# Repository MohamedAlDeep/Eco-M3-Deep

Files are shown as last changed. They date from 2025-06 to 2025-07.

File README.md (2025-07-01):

# Eco M3 Deep
It is my custom built 3D printer, with all custom 3D printed parts with large bed area.

I made this printer as it would help in making other projects as i don't have direct access to one, and i am interested more on hackclub events projects & science projects which constantly need custom 3D printed parts.

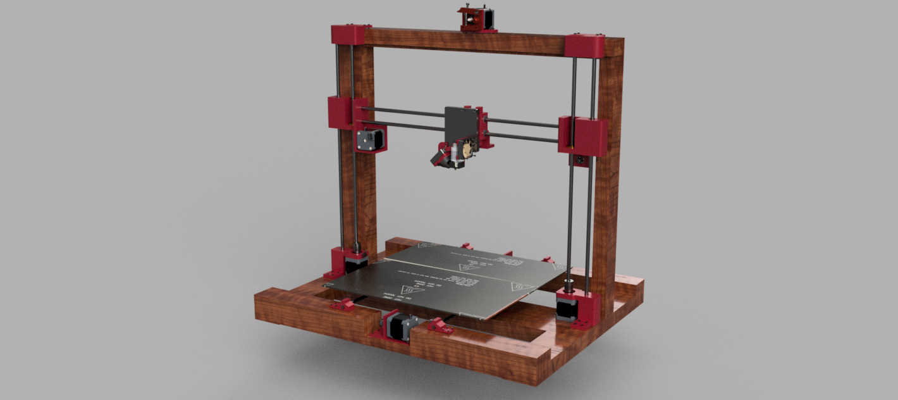
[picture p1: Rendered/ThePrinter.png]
The Printer


## Features 
    - Simplicity
    - Large Bed size with area of 40cmx40cm
    - Remote Extruder
    - The structure & large bed mount are made from wood to reduce cost
    - Expandable design for future additions

## Assembly
1. Mounts 

    - It is simple, start by putting linear bearings into the mounts specifically the moving z axis and the hotend mounts. 
2. Attachments
    -  Screw the hotend
    - Attach mechanical stops with the y axis motor, the same applies to the z axis bottom mount.
    - Screw the x axis bed motor onto its place.
    - Add the pulleys onto the motors shafts and onto a 3D printed small 8mm shaft that is connected to a 8mm bearing.
3. Structure
    - Make 7x 2x3cm wooden part with length of 50cm, put them together as in the image.
4. Axes assembly
    - Z axis
        - Connect the bottom z axis motor to the coupler and the coupler to the T8 lead screw.
        - Connect the T8 screw nut onto its place on the movable z axis middle mount.
        - Connect the upper z mount that has an 8mm bearing into the T8 screw.
        - Stabalize the structure by connecting the linear rod into its place through the three mounts.
        - The same applies on the other side
    - X axis
        - Mount the motors
        - Place the linear rods into their mounts 
        - Put the linear bearings into thier movable mounts.
        - Screw the movable mounts onto a 45x45cm wooden bed.
    - Y axis
        - Mount the hotend into its place
        - Connect the linear bearings
        - Screw the hotend mount onto the movable part.
5. Mechanism
    - Attach the timing belts to the mounts for z - x - y axes.
    - Connect all cables to the mainboard
6. Firmware
    - Install Marlin 2.0 firmware

## Bill of Materials (BOM)
| Name | Description | Unit Price | Quantity | Total Price | Total in USD | Link |
|---|---|---|---|---|---|---|
| Stepper Motors | Nema 17 Stepper motor 17hs8401s Usongshine 48mm (Black) | 825 | 5 | 4125 | 83.49 | [Link](https://www.amazon.eg/-/en/gp/product/B0969CFKLM/ref=ox_sc_act_title_1?smid=A26I4OU0GDWZ7W&psc=1) |
| Linear Rods | Stainless Steel Linear Rod (8mm, 1m) | 260 | 3 | 780 | 15.79 | [Link](https://www.amazon.eg/-/en/gp/product/B09Z3QJF1P/ref=ox_sc_act_title_2?smid=A3G2ZVUBEERR0N&psc=1) |
| Pulleys | GT2 Timing Pulley 20 teeth Bore 5mm 2 Pcs | 149 | 2 | 298 | 6.03 | [Link](https://www.amazon.eg/-/en/gp/product/B0969JNT3G/ref=ox_sc_act_title_2?smid=A26I4OU0GDWZ7W&psc=1) |
| Remote Extruder | Comgrow Upgraded Replacement Aluminum MK8 Extruder Drive Feed for Creality CR-10, CR-10S, CR-10 S4, and CR-10 S5 | 595.96 | 1 | 595.96 | 12.06 | [Link](https://www.amazon.eg/-/en/gp/product/B07BBPFFVD/ref=ox_sc_act_title_1?smid=A22MDF17B7GE04&psc=1) |
| End Stop | 3D Printer Mechanical End Stop Switch Module | 89.99 | 3 | 269.9 | 5.46 | [Link](https://www.amazon.eg/-/en/gp/product/B0968R6TJ8/ref=ox_sc_act_title_5?smid=A1G5VPUVPXBMQ6&psc=1) |
| Motors Couplers | 3D Printer and Cnc Stepper Motor Flexible Coupling Coupler (5 to 8mm) | 105 | 2 | 210 | 4.25 | [Link](https://www.amazon.eg/-/en/gp/product/B0968ZBB2J/ref=ox_sc_act_title_6?smid=A26I4OU0GDWZ7W&psc=1) |
| T8 Lead Screw | T8 Thread Lead Screw 8mm, 2mm with Brass Nut (500mm) | 295 | 2 | 590 | 11.94 | [Link](https://www.amazon.eg/-/en/gp/product/B0969HF39S/ref=ox_sc_act_title_7?smid=A22MDF17B7GE04&psc=1) |
| Linear Bearings | Linear Bearings 3D Printer, LM8UU, 8mm, 6 Pieces | 249 | 2 | 498 | 10.08 | [Link](https://www.amazon.eg/-/en/gp/product/B0968Y5C94/ref=ox_sc_act_title_8?smid=A3HOVOH12T9VII&psc=1) |
| Timing Belt | adp GT2 Timing belt 2mm pitch 6mm wide Rubber Opening Timing Belt For 3D Printer - 2M | 275 | 1 | 275 | 5.57 | [Link](https://www.amazon.eg/-/en/gp/product/B099DC5JK5/ref=ox_sc_act_title_9?smid=A26I4OU0GDWZ7W&psc=1) |
| Hot End | CUHAWUDBA 3D Full Metal J-Head CR10 Hotend Extruder Kit Hot End Kit for CR10 10S Bowden Extruder 24V 40W 3D Printer Parts | 610 | 1 | 610 | 12.35 | [Link](https://www.amazon.eg/-/en/gp/product/B082WQVCKT/ref=ox_sc_act_title_10?smid=A3HOVOH12T9VII&psc=1) |
| Power Supply | Power Supply 24V 10A. | 595 | 1 | 595 | 12.04 | [Link](https://www.amazon.eg/-/en/gp/product/B0DR633KMW/ref=ox_sc_act_title_11?smid=A2DMKAT7ZKLGQN&psc=1) |
| SKR 1.4 | SKR V1.4 TURBO | 2,999.00 | 1 | 2,999.00 | 60.70 | [Link](https://www.amazon.eg/-/en/gp/product/B09BMGXJ8S/ref=ox_sc_act_title_12?smid=A3HOVOH12T9VII&psc=1) |
| Stepper Motors Drivers | TMC2209 V2 Stepper Motor Driver | 480 | 4 | 1920 | 38.86 | [Link](https://www.amazon.eg/-/en/gp/product/B0DJZL2XPQ/ref=ox_sc_act_title_15?smid=ANKKSL5YJGFAH&psc=1) |
| Heated Bed | Aluminum Heated Bed for 3D Printer (400x200x3mm) | 500 | 2 | 1000 | 20.24 | [Link](https://www.amazon.eg/-/en/gp/product/B099D8ZBVM/ref=ox_sc_act_title_1?smid=A2TUHD4CZOFOST&psc=1) |
| Bed Leveling Screws | 3D Printer Bed Leveling M3 Screw with Spring and Hand Knob 5 Pieces | 155 | 2 | 310 | 6.27 | [Link](https://www.amazon.eg/-/en/gp/product/B0968XHW56/ref=ewc_pr_img_1?smid=A22MDF17B7GE04&psc=1) |
| Cooling Fan | 3D 4010 Brushless Cooling Fan, 24v DC with Ball Bearing 2pin Connector | 90 | 2 | 180 | 3.64 | [Link](https://www.amazon.eg/-/en/gp/product/B0DJ9R2ZJ3/ref=ewc_pr_img_1?smid=A2DMKAT7ZKLGQN&psc=1) |
| Thermistors | 100K Ohm NTC 3950 Thermistors Temperature Sensor with Cable Dupont Head for Reprap Mendel MK2A MK2B Heated Bed 3D Printers Parts | 100 | 3 | 300 | 6.07 | [Link](https://www.amazon.eg/-/en/gp/product/B09MSPWTM5/ref=ewc_pr_img_1?smid=A26I4OU0GDWZ7W&psc=1) |
| 5mm Bearings | uxcell 625-2RS Deep Groove Ball Bearing 5x16x5mm Double Sealed ABEC-3 Bearings 10-Pack | 216 | 1 | 216 | 4.37 | [Link](https://www.amazon.eg/-/en/gp/product/B07TML6YP4/ref=ox_sc_act_title_1?smid=A24L91U83A8RCR&psc=1) |

**Total:** 15,771.86 (319.21 USD)  
**Total In USD (18/6/2025):** 320$

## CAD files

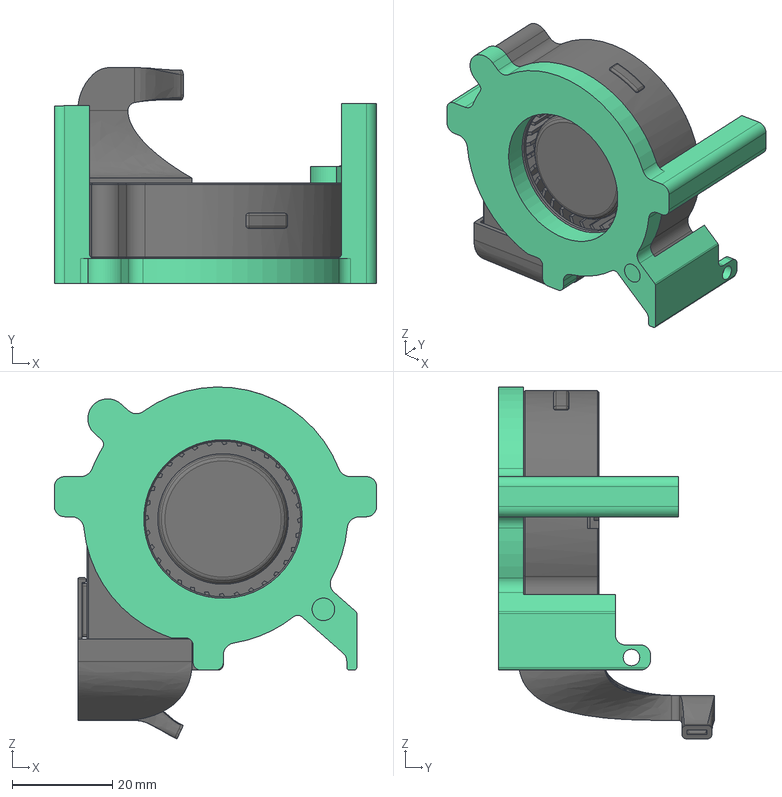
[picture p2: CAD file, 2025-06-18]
CAD/Part Cooling Fan.step
64.2 x 43.0 x 70.2 mm

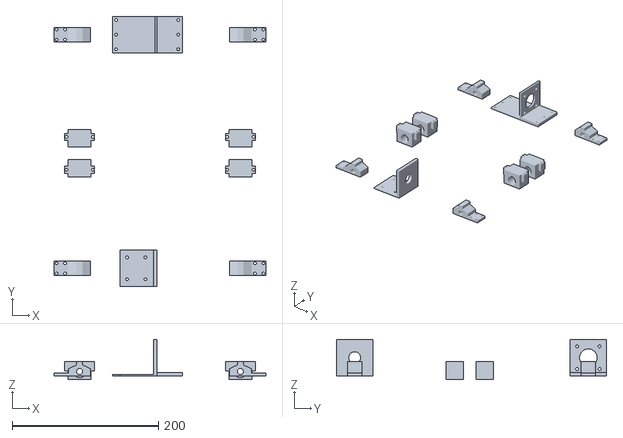
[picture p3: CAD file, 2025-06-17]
CAD/X axis/Motor Mount X Axis v14.stl
290.3 x 370.0 x 55.0

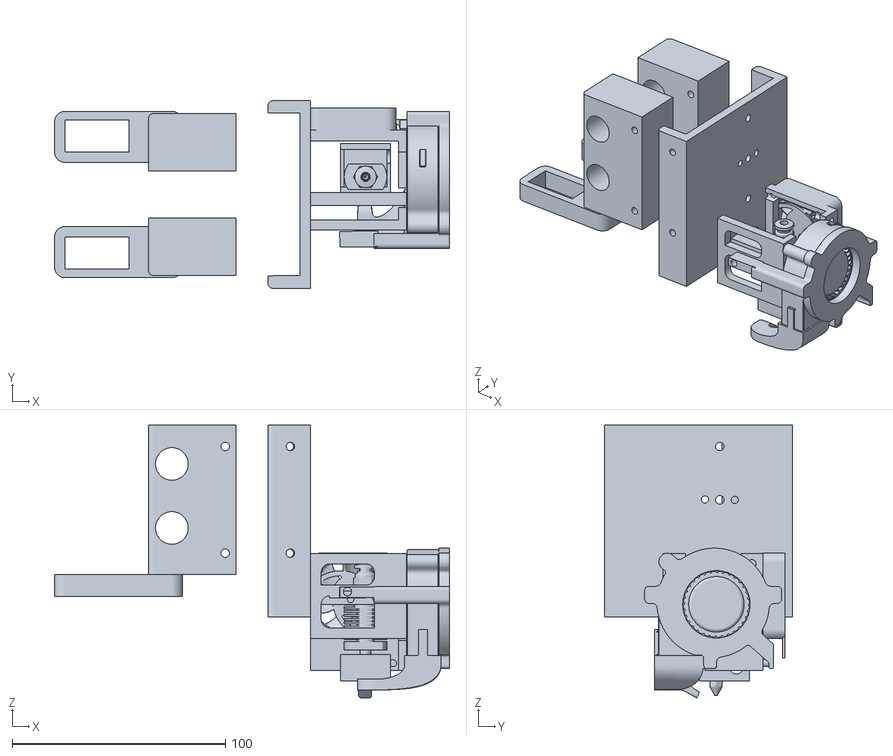
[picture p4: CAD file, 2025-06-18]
CAD/Y axis/HotEnd (Y Axis) v27.stl
185.1 x 88.0 x 127.8

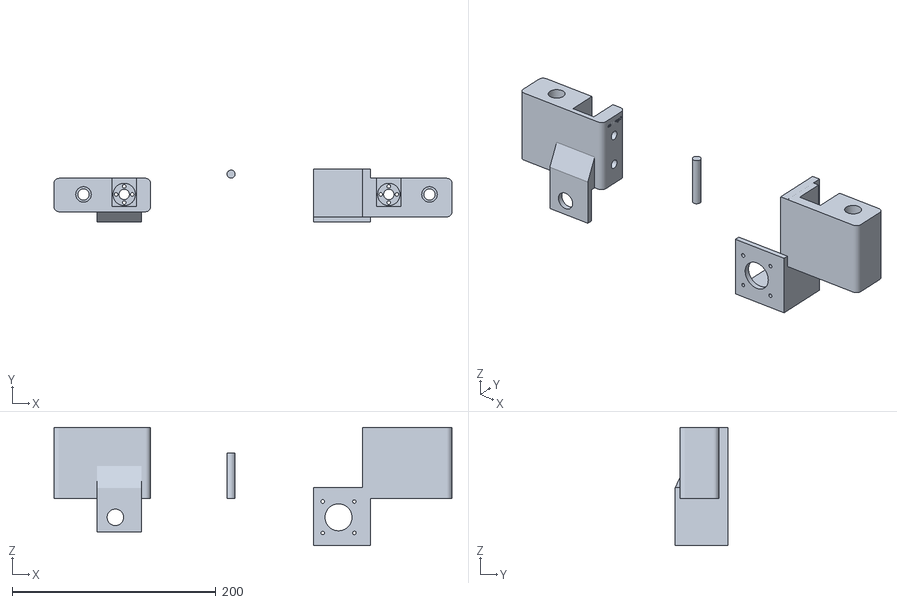
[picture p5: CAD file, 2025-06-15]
CAD/Z axis/Middle Mount Z axis (X axis Holder) v12.stl
391.1 x 52.1 x 116.0

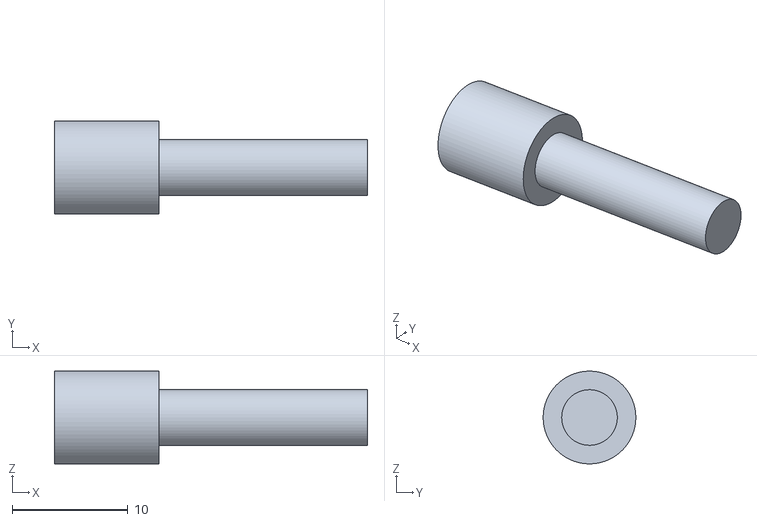
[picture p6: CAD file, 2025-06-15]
CAD/X axis/Pulley Holder v3.stl
27.0 x 8.00 x 7.99

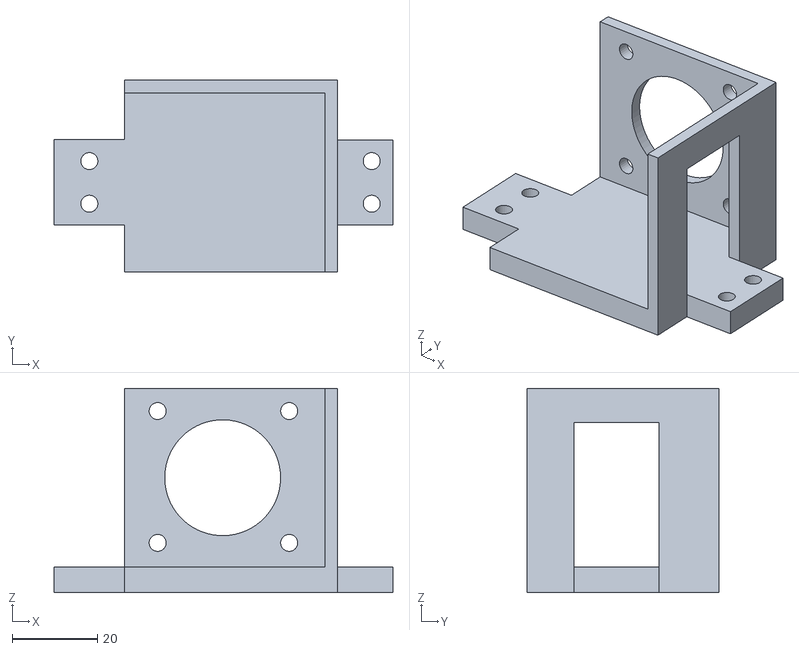
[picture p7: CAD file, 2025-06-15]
CAD/Y axis/Bowden Extruder Mount v2.stl
79.6 x 45.0 x 48.0

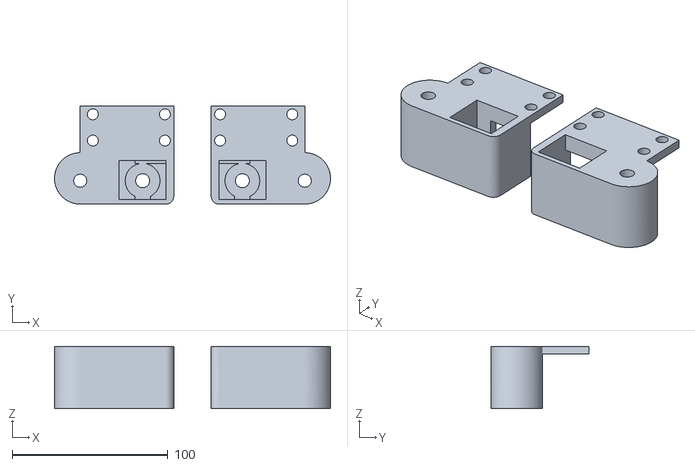
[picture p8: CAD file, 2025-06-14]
CAD/Z axis/Upper Mount Z axis v4.stl
177.0 x 63.0 x 40.0

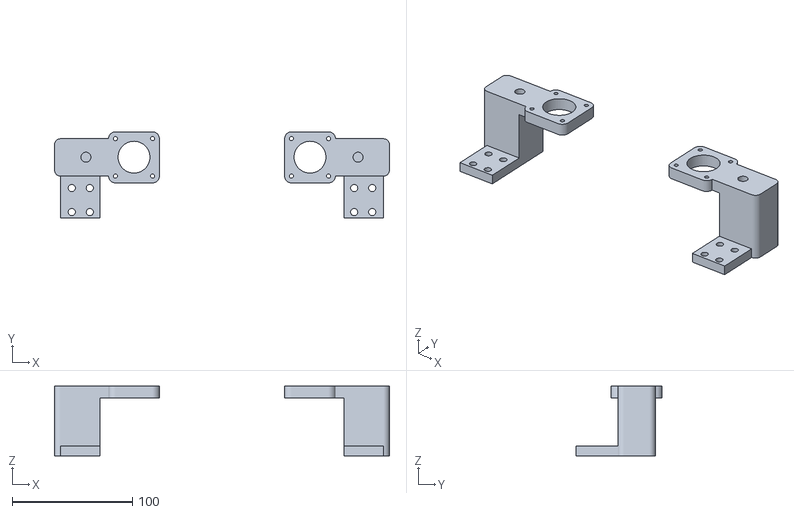
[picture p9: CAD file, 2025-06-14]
CAD/Z axis/Bottom Mount (Z axis Steppers) v7.stl
278.8 x 71.9 x 58.0

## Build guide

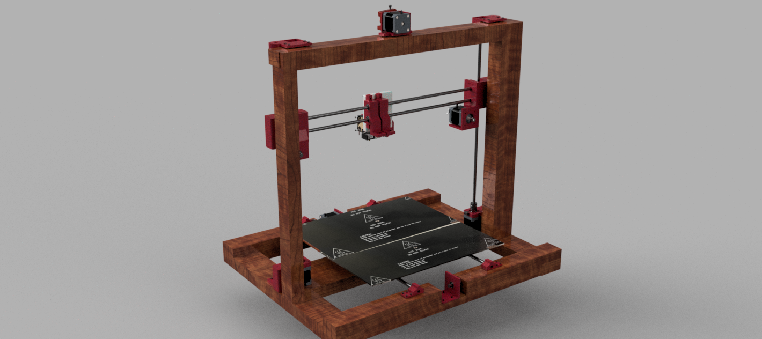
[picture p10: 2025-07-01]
Rendered/ThePrinter_12.png

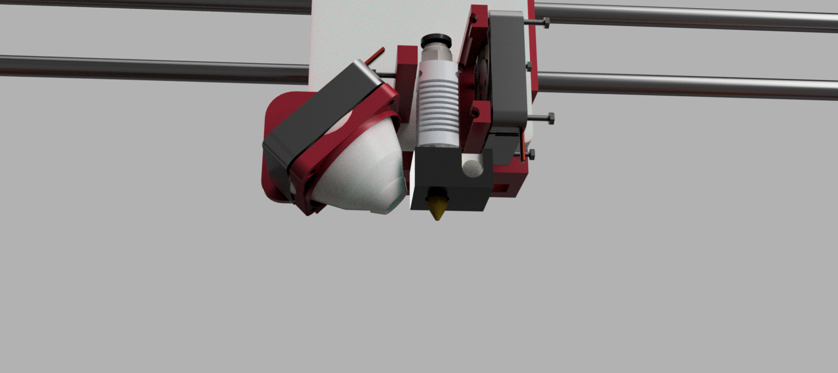
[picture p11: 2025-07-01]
Rendered/ThePrinter_10.png

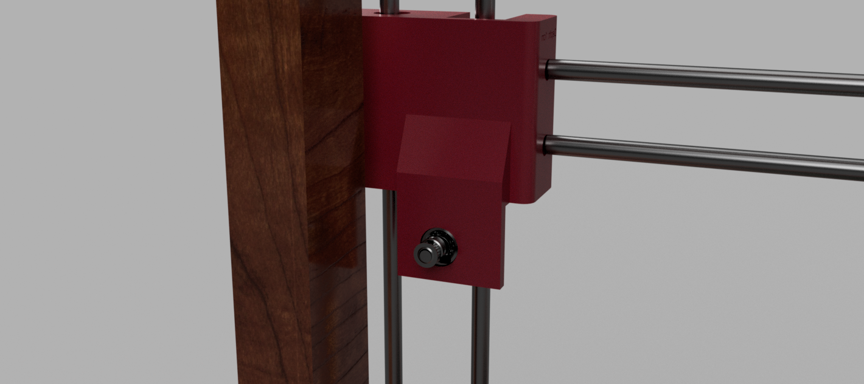
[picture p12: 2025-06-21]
Rendered/ThePrinter_13.png

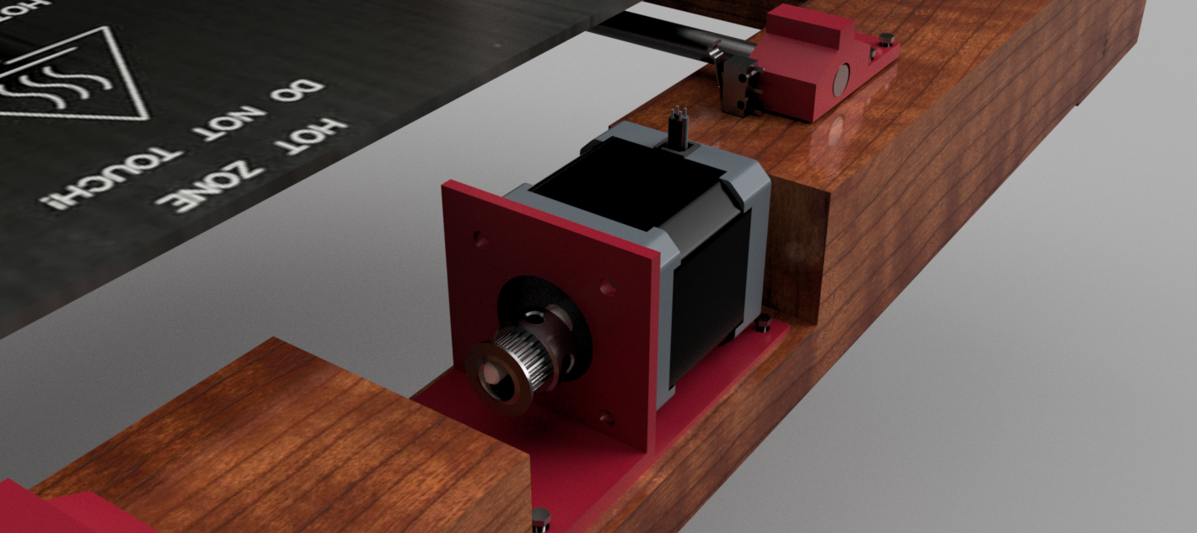
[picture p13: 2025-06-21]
Rendered/ThePrinter_11.png

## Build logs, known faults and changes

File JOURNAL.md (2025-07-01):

---
title: "Eco M3 Deep"
author: "Mohamed Samir"
description: "Custom Built, Cheap, large size 3D printer"
created_at: "2025-06-6"
---

Total time spent: 64h

## Day 1 (06/6) 
> Spent: 4h

I made a lot of research on how 3D printers work, in addition to their different types and what are the different components they share and advantages and disadvantages in components types.

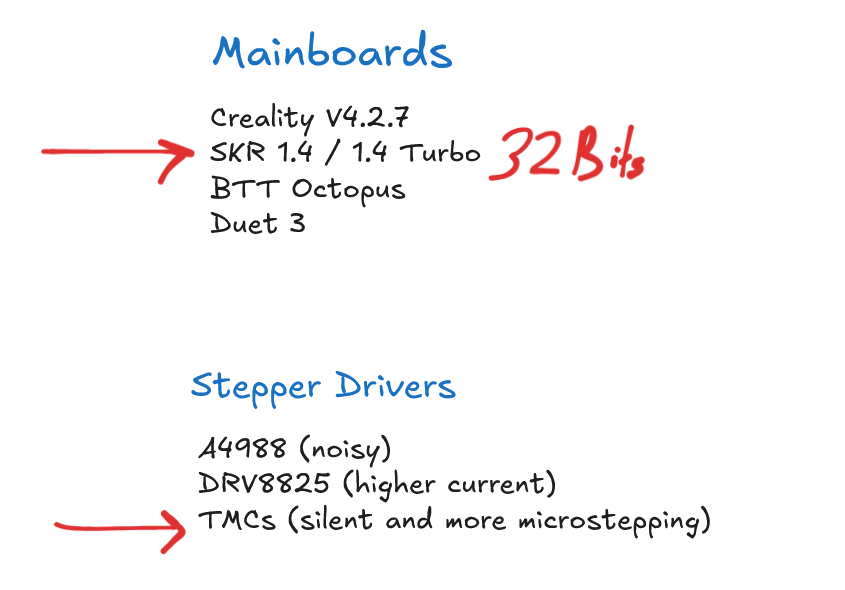
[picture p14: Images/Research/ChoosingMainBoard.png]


I couldn't find any other on amazon other than the SKR 1.4, which is a great option for as it is 32Bit and enables mutliple beds, i chose the TMC2209 drivers as they enable high accuracy microstepping, which i am planning to combine with low size nozzle (0.3mm) in building high resolution prints.

## Day 2 (07/6)
> Spent: 5h

Continued watching more videos, i was interested in simple cartesian bed slingers, in which i searched about how they are assembled and different design strategies.

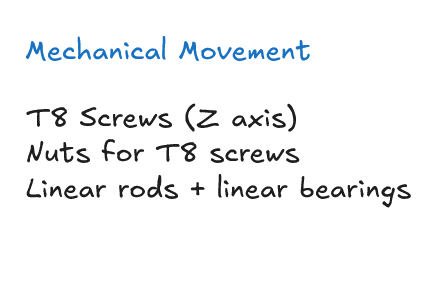
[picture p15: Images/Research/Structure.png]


I chose the standard 8mm diameter for both the T8 lead screw and the linear rods, based on that i chose the 8mm bore 20 teeth pulleys. 

I searched for all of that on AliExpress but they were much more expensive than in the local amazon.eg site. 

## Day 3 (08/6)
> Spent: 5h

Built ideas about the design and materials needed, i chose a wooden frame & bed mount as other materials like linear rails with linear wheel bearings raise the cost.

I found different types of timing belt & chose the compatible GT2 2mm Pitch belt with width of 6mm.

Found 100k NTC thermistors, i wanted three of them for my two beds and hotend.

I also found a 24v cooling fan on amazon for the hotend heatsink, i found bed leveling kit.

## Day 4 (09/6)
> Spent: 9h

Chose the bed size to be 40x40cm with total structural dimensions of 50cmx50cm.

I found this bed on amazon which is 40x20, so i decided to get two of it and put them next to each other.
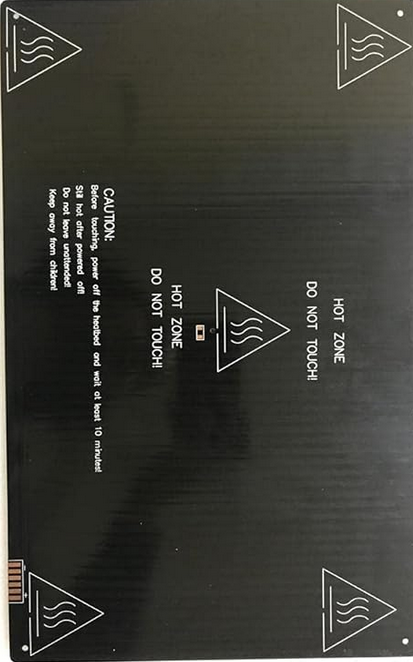
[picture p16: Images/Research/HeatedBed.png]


For the electronics i chose it to be a simple single hotend with bowden extruder as i focus more on speed printing, with SKR 1.4 mainboard, with 4 TMC 2209s that are connected to the nema 17 stepper motors, for the dual z axis motors i decided to run them in parallel with the same driver, and for the bed leveling i decided to leave as the manual leveling screw-spring method.
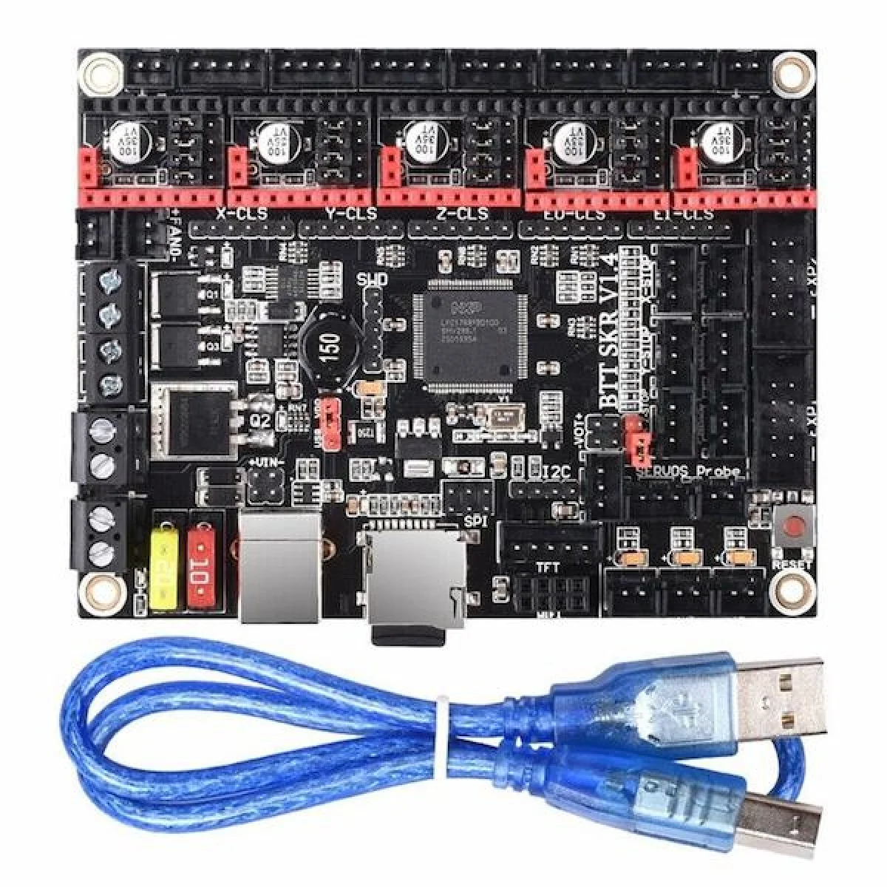
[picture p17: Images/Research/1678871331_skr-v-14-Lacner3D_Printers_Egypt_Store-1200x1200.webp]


The motors of choice are the 17HS8401S with height of 48mm, as they have optimal tourque for operation & they are widely used in 3D printers.
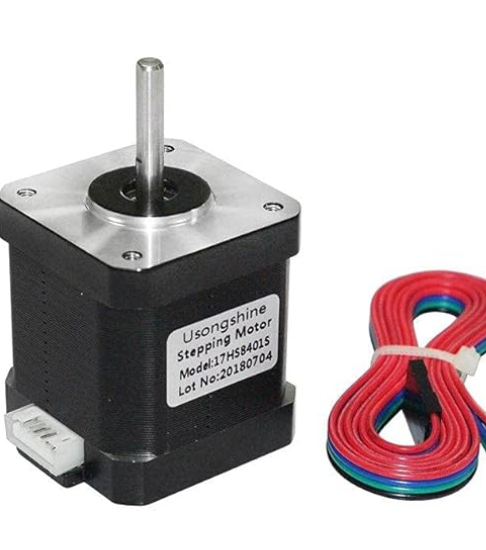
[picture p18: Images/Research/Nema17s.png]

## Day 5 (10/6)
> Spent: 8h

Started desiging the x axis mount, i had to go through various implementations and modifications 

*The first version of the design*
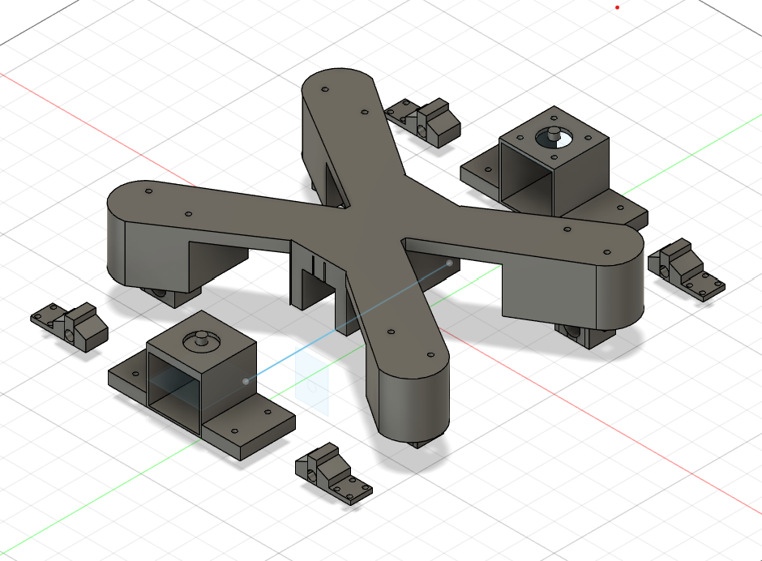
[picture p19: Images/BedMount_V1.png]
Bed Mount first


After putting work on the first design i realised how non feasable it was. Which made me thinking about a much better abstraction. 

*Final Version*

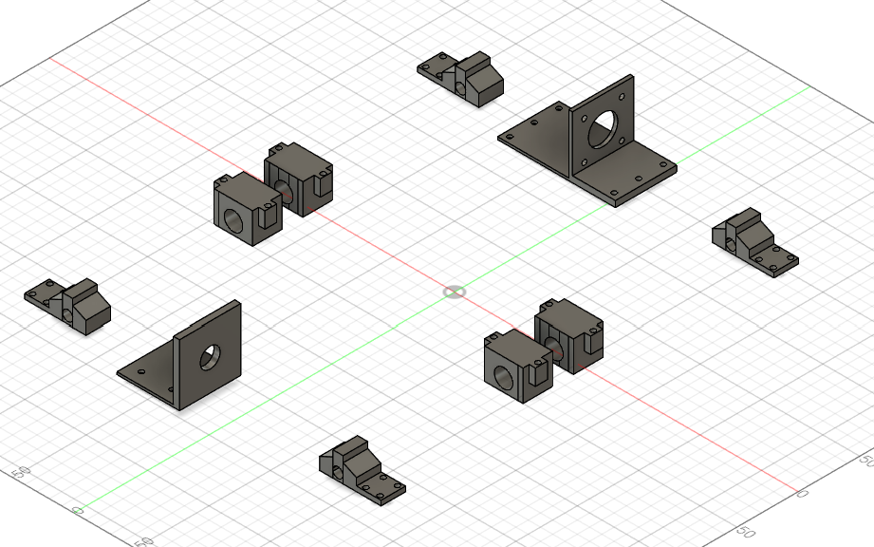
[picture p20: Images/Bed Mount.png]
Bed Mount


This structure is made of two symmetrical groups, it has two mounts for the 8mm linear rods on each side, with a pulley + bearing mount and motor mount on the top far side, which are going to hold the timing belt.

The parts at the center are the movable parts that have LM8UU (8mm) linear bearings with holes inside them exactly at the same size of each one of them, those parts are then connected to a wooden sheet for both mounting the heating beds and insulating excess heat. 
## Day 6 (11/6)
> Spent: 10h

I started working on the z axis.

This is the bottom mount for the dual z axis motors, it has four 4mm holes for screwing it on a wood part, the motor is put under the upper part which has a height of exactly 48mm to match up with the motor, then a coupler is used to connect the motor shaft with the T8 lead screw (8mm). Then the Linear rods are put into their holes vertically.

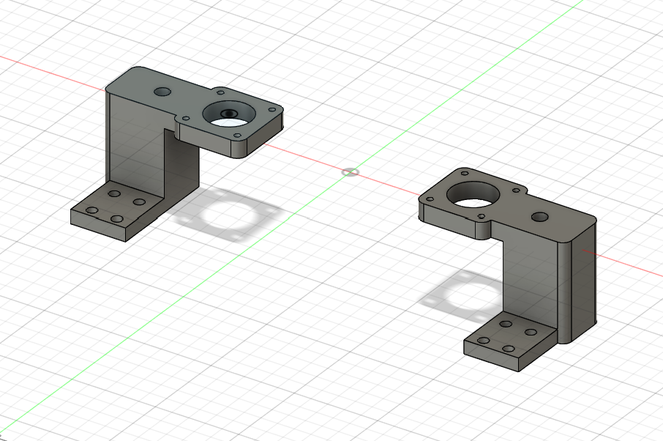
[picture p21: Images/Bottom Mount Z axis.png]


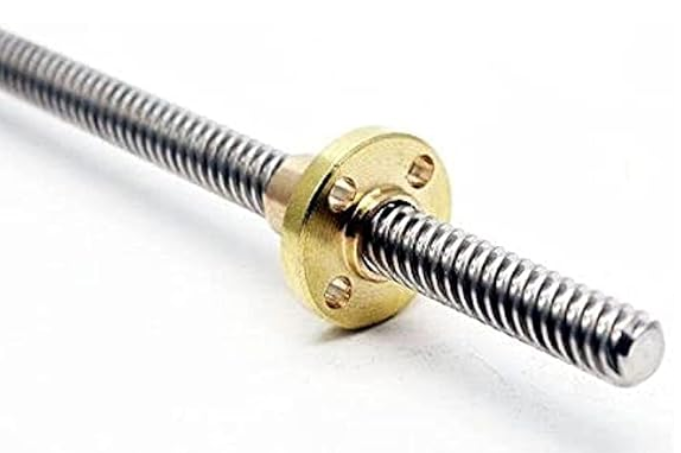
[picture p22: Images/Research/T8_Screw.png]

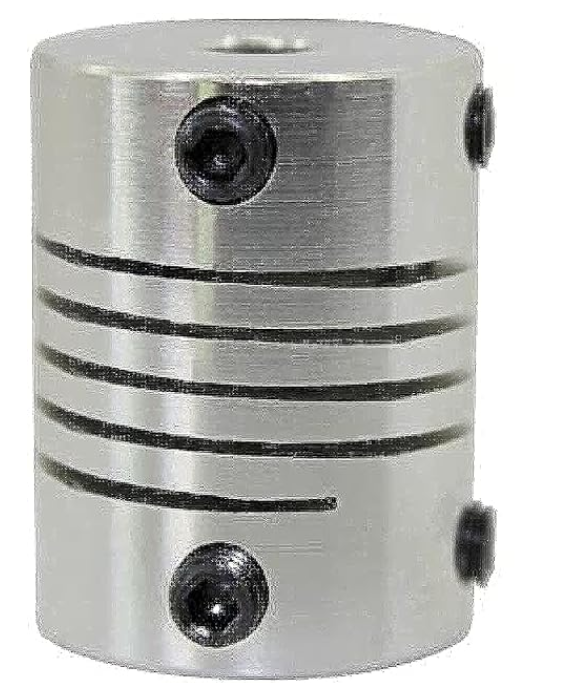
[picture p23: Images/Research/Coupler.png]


The second part is the middle moving part that holds the y axis motor to the pulley and also has the screw mount that is used in moving up & down by the rotating T8 screw. I made a small 8mm shaft that would be inserted into the pulley and connected to the part on the left.

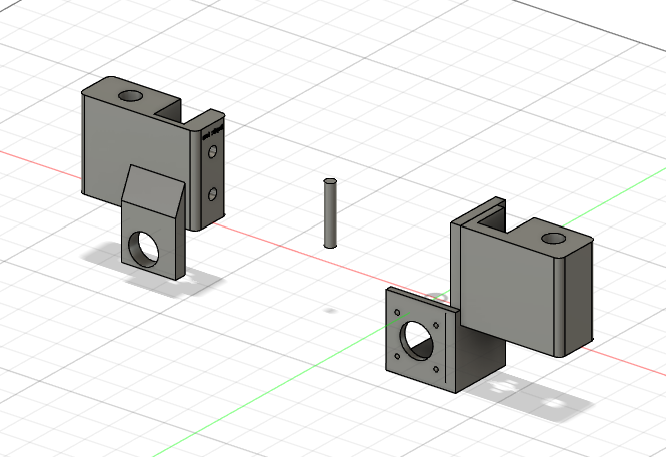
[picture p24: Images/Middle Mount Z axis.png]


## Day 7 (12/6)
> Spent: 7h

Finalized the z axis mounts. The upper mount which has an 8mm bearing to stabalize the T8 screw with the screw holes on the top to be secured on the wooden structure. 

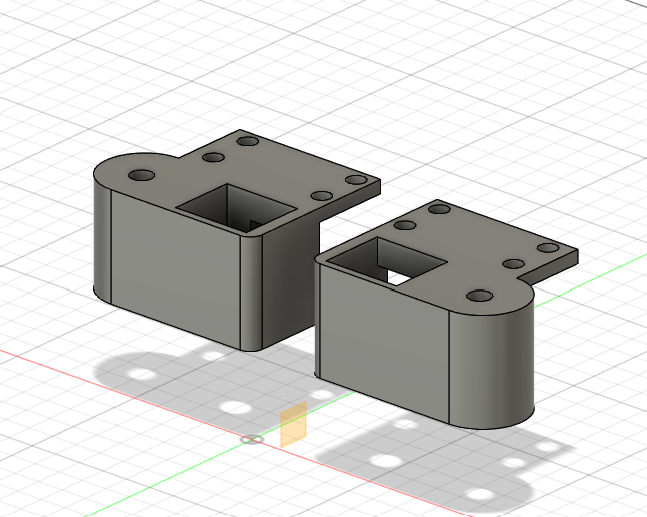
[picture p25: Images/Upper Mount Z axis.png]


I also started searching for the materials on different shopping websites, at first i checked aliexpress but i found the linear rails they sell are expensive in addition to the shipping cost. I decided to search for the materials on amazon.eg which had all materials but some were different or out of stock, like the hotend which is the CR10 Bowden extruder kit. which i had to choose because the site didn't have any other 24v hotends.

## Day 8 (13/6)
> Spent: 13h

I designed the extruder mount with the hotend mount.

I decided to put the extruder on the top of the structure with screw holes on the bottom.

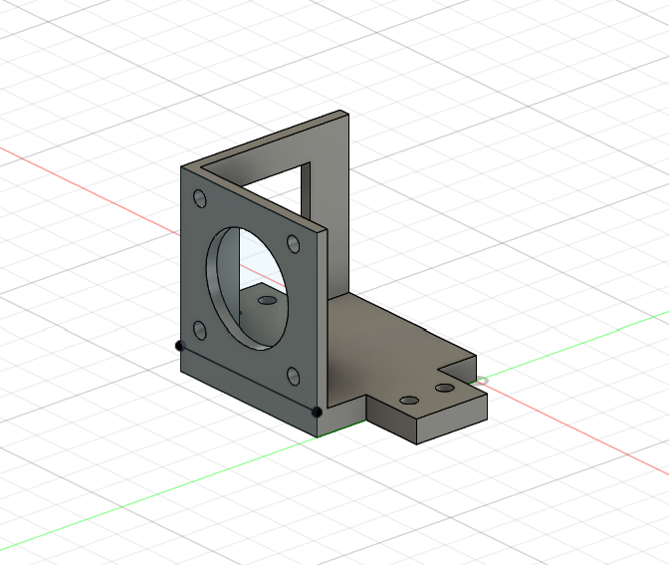
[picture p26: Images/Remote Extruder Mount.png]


For the hotend mount i made 2 holes for mounting the CR10 hotend and additional holes for future modifications.

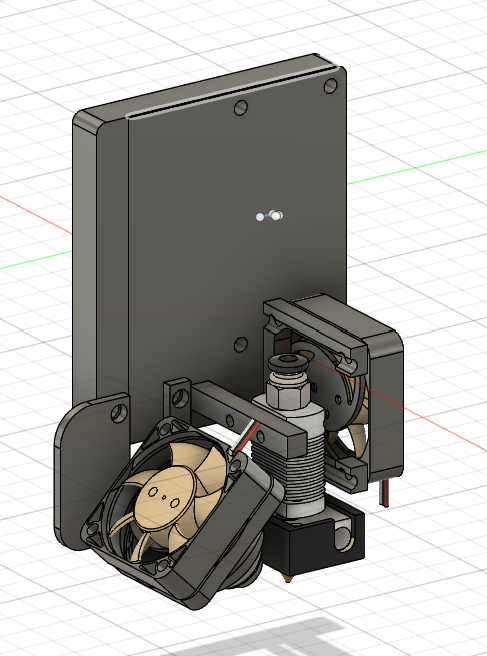
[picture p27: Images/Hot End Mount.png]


 The backward side of the mount, has two square hollow structures that are used for holding the moving timing belt.

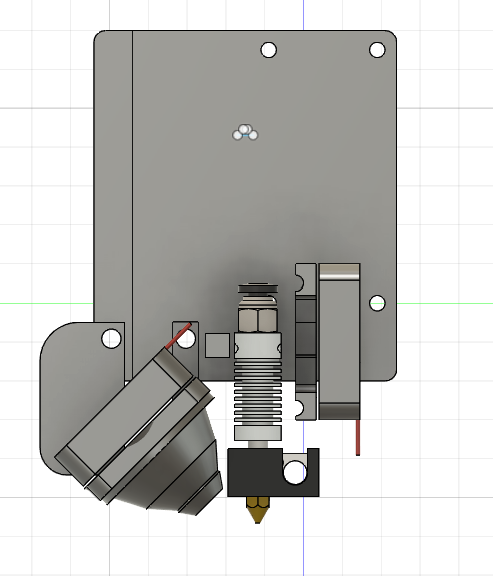
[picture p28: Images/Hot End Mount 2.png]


### The Assembly 
1. Mounts 

    - It is simple, start by putting linear bearings into the mounts specifically the moving z axis and the hotend mounts. 
2. Attachments
    -  Screw the hotend
    - Attach mechanical stops with the y axis motor, the same applies to the z axis bottom mount.
    - Screw the x axis bed motor onto its place.
    - Add the pulleys onto the motors shafts and onto a 3D printed small 8mm shaft that is connected to a 8mm bearing.
3. Structure
    - Make 7x 2x3cm wooden part with length of 50cm, put them together as in the image.
4. Axes assembly
    - Z axis
        - Connect the bottom z axis motor to the coupler and the coupler to the T8 lead screw.
        - Connect the T8 screw nut onto its place on the movable z axis middle mount.
        - Connect the upper z mount that has an 8mm bearing into the T8 screw.
        - Stabalize the structure by connecting the linear rod into its place through the three mounts.
        - The same applies on the other side
    - X axis
        - Mount the motors
        - Place the linear rods into their mounts 
        - Put the linear bearings into thier movable mounts.
        - Screw the movable mounts onto a 45x45cm wooden bed.
    - Y axis
        - Mount the hotend into its place
        - Connect the linear bearings
        - Screw the hotend mount onto the movable part.
5. Mechanism
    - Attach the timing belts to the mounts for z - x - y axes.
    - Connect all cables to the mainboard
6. Firmware
    - Install Marlin 2.0 firmware

## Day 9 (14/6)
> Spent: 3h

Started finalizing the printer and assembeld all parts on the software.
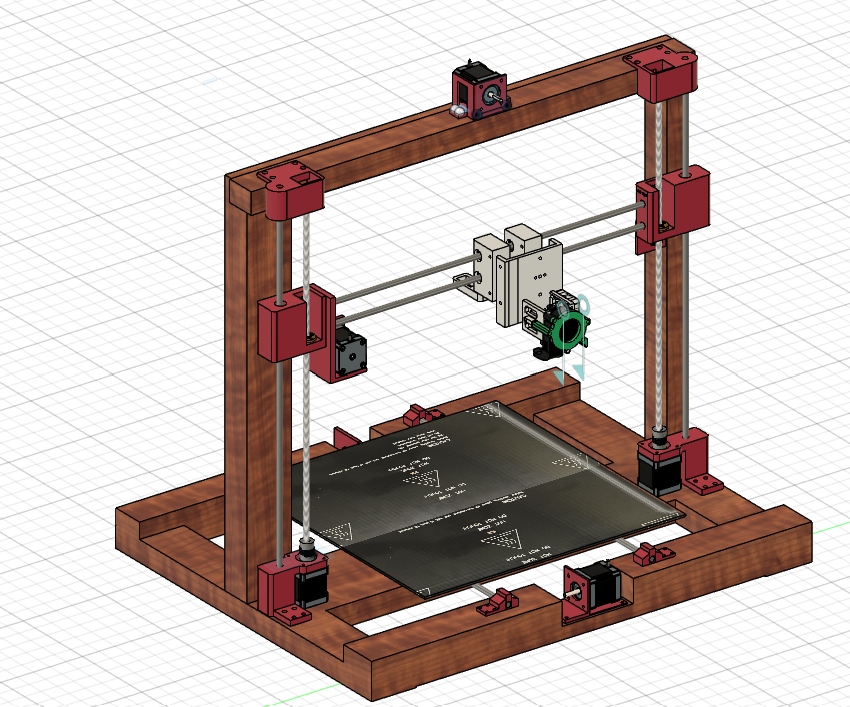
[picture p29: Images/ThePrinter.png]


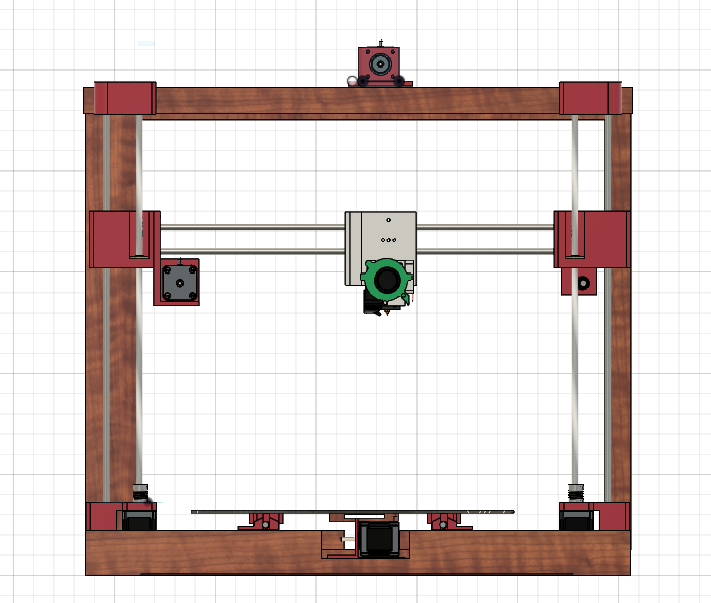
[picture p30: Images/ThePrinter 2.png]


### Images

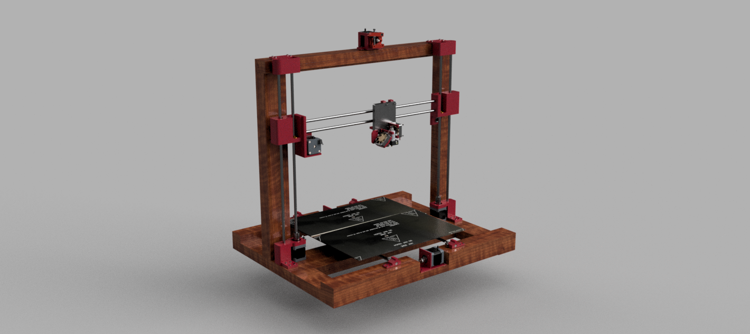
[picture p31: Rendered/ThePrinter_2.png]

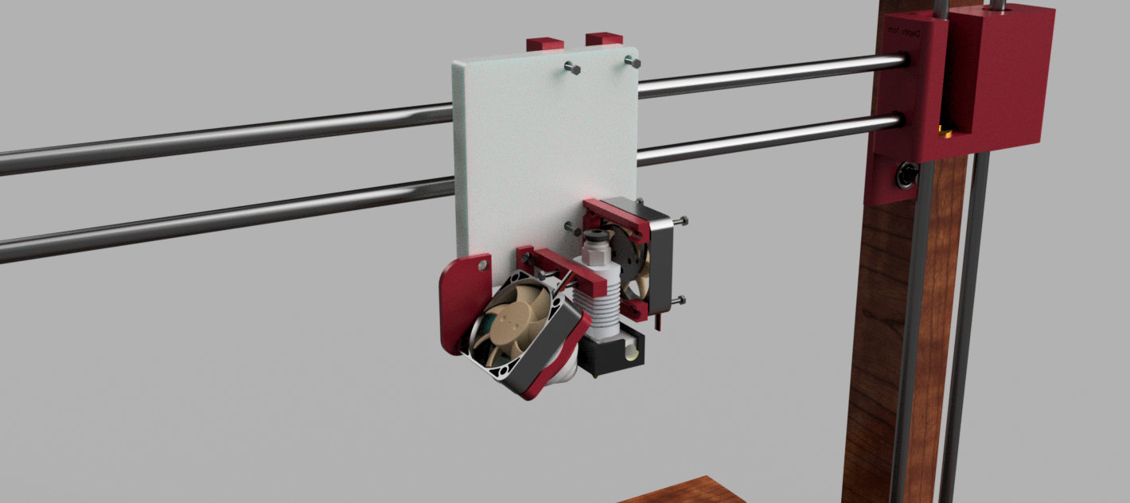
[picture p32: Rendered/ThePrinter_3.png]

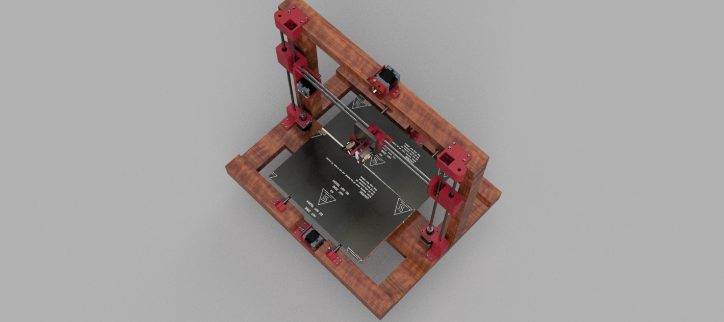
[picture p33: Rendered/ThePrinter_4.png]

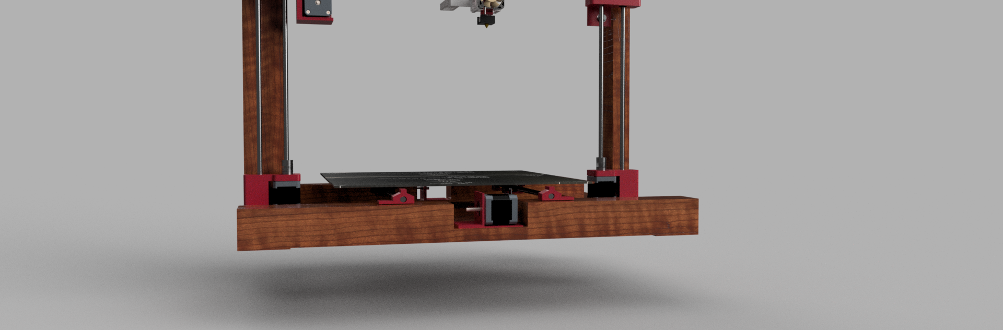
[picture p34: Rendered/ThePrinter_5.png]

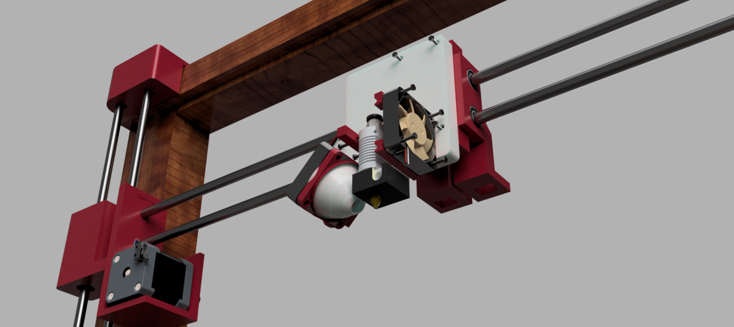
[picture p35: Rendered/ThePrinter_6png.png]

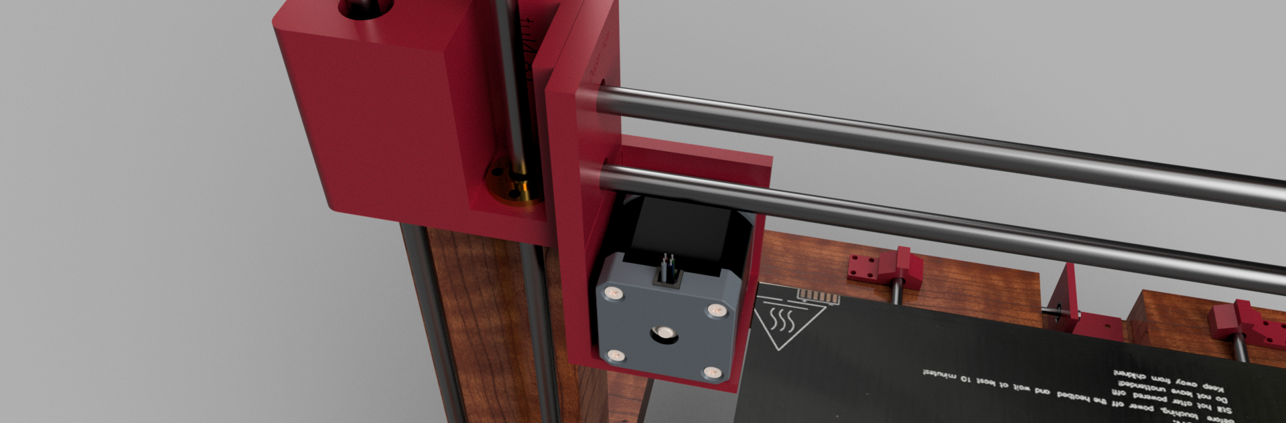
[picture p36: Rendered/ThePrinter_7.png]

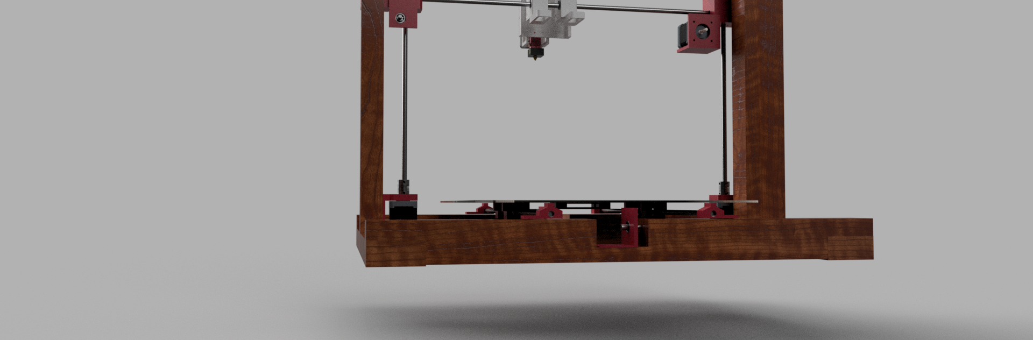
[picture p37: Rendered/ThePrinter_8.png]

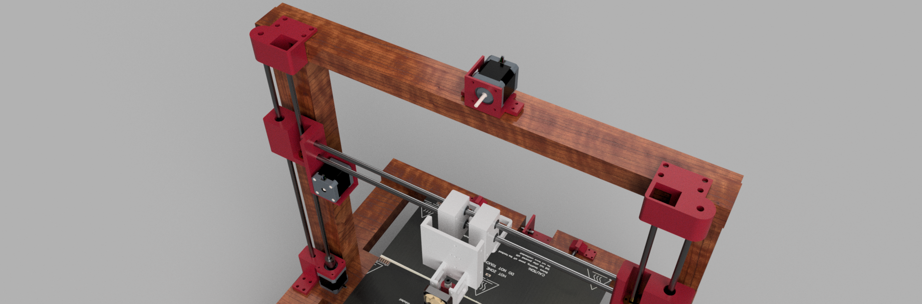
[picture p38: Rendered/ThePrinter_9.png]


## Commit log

2025-06-14 Added Readme
    [BOM.csv]
2025-06-15 Added The STL for printer
2025-06-18 edit BOM
    [BOM.csv]
2025-06-18 Added costs in USD
    [BOM.csv]
2025-06-26 fixed f3z and design
    [BOM.csv]
2025-07-01 Fixed BOM
    [BOM.csv]
